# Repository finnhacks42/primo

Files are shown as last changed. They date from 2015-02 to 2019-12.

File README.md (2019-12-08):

KinderBot
=====

Contains design files and code for my version of the Primo robotic platform for young kids www.primo.io licenced under CC by-nc-sa 4.0 International
## Components
### Board
   - laser cut xxx and yyy in 3mm ply or bamboo
   - laser cut zzz in 1.5mm clear acrylic
   - 3d print 4 off zzz
   - 1 colorsense PCB
   - Arduino mega
   - HC05 serial bluetooth module
   - 16 rgb leds
   - 16 red leds

### Robot
   - Kinder surprise egg
   - laser cut zzz of 3mm ply
   - Arduino pro micro 
   - 2 gear motors 3-6V with tyres
   - HC05 serial bluetooth module
   - H-Bridge IC (sn75441one)
   - 1.1K resistor
   - 1.2K resistor
   - 2 12pin female header
   - 2 2pin male header
   - Battery holder for 4xAA

## Pairing Bluetooth modules
Once you have all your components ready, the first step set up the two HC-05 bluetooth modules to automatically pair with one another when they are turned on. We do this now as it is easier to setup and debug with both Arduinos handy than when they are plugged into the board/robot. We will configure the module for the board as the master and the module for the robot as the slave. 

   1) Get a permanent marker and write S for slave on one module and M for master on the other. Do it now, trust me, otherwise you will configure them and then forget which is which.
   2) Using the Arduino pro-micro for your bot, construct the circuit below on a breadboard.

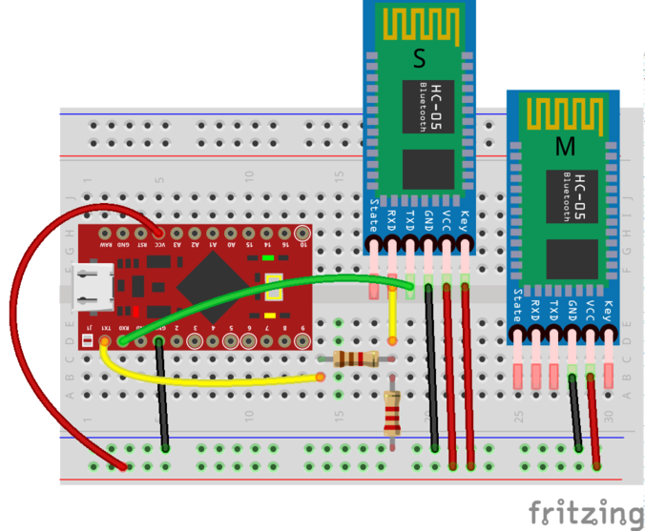
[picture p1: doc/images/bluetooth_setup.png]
bluetooth setup


Note that different manufacturers of the HC-05 breakout boards have used slightly different variants of pin orderings. On my board they `key` pin is not broken out. To temporally pull it high while programming the chip in AT mode I have just wedged a jumper wire under the protective plastic coating. Alternatively you can solder a wire directly to the pad on the bluetooth chip (see image below).

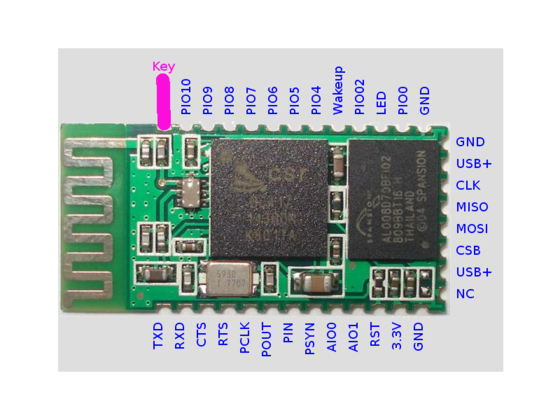
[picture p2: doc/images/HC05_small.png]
hc05


   3) Load the [bluetooth setup script](/code/bluetooth/bluetoothSetup/bluetoothSetup.ino) onto the arduino and open the serial monitor. If all goes well you should get an output like this:
   
   4) Copy the address of the slave into a text editor and replace all : with ,
   
   5) Unplug the arduino and swap the position of the master and slave modules. Edit the bluetooth setup script to setup the master module and re-upload the script to the arduino. Again if all goes well you should see ...
   
### Debugging
The bluetooth modules are setup by first putting them in AT mode and then sending AT commands to configure them. The script simply sends AT commands from the Arduino to the bluetooth module. If the steps above did not work ...
   1) Check if the module is in AT mode. If the module being configured (the one closest to the breadboard) is sucessfully in AT mode it should be flashing slowly ~ once per second when powered. If both modules are flashing rapidly, double check the wiring to the key pin. Ensure that the key pin is connected before you power up the module. 
   2) If the module is flashing slowly but you get nothing back from the AT commands check that RX/TX are wired correctly. TX0 on the arduino should be connected to RX on the bluetooth and RX0 on the arduino to TX on the bluetooth module.
   3) If the module is flashing slowly but you get garbage printed in the serial monitor, check that you serial termial baud rate is set to 9600 and line ending to NL & CR.
   4) If the module is flashing slowly but some AT command errors try running the script again. If that fails you may have to experiment with a different sequence of AT commands see xxx for an explaination of AT codes. 

## Assembly

### Board

### Robot

## Programming & Calibration

### Board

### Robot

We now need to

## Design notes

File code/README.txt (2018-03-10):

Ensure circuit board is properly secured before beginning calibration.

Rough order of steps to callibrate the board.

First test indicator leds are working.

Then test rgb leds are working

Then test light dependent resistors are working

Then upload colorsense and run python script to learn colors - paste results into primoOpticalBoard

Upload code to primoOpticalBoard - and you should correctly be identifying the tiles and sending out code.

TODO: update color_distance.py to use utils and to work from the board or a file.

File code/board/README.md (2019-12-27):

# Board 

## Assembly

## Test & Configure

   1. Run `indicatorLEDTest_PCB` and check each red indicator LED flashes in turn. 

   2. Place a tile in each slot in the board (doesn't matter what colour). Run `LDRTest` and open up the serial monitor (at 9600 baud). You should see something like:

      ```  python
      0,610
      0,758
      0,637
      0,554
      0,580
      0,536
      0,786
      0,708
      0,609
      0,549
      0,510
      0,556
      0,722
      1,731
      0,771
      0,735
      ```
      These numbers are the values of each LDR with the corresponding RGB-LED on/off respectively. The first number should be < 10 and the second > 150.

   3. Load the `CalibrateColours` sketch onto the board and run `python read.py` in the terminal. You should see `PLEASE SET BOARD TO CONFIGURATION: Red|Green|Blue|Yellow. Press any key to continue` in the terminal. This means set the board up like this:

   4. When the terminal reports `Shuffle. Press any key to continue`, move the tiles around so that each tile is in a new spot - but within the same column (ie which colour is in which column is unchanged). 

   5. Continue for each board configuration. This generates the data from which to compute what LDR responses correspond to each colour of tile.  When all is complete, you should get an output like this;

      ```
      int average_brightness[16][3] = {
         {507,588,256},
         {684,687,365},
         {709,643,295},
         {652,670,342},
         {694,410,420},
         {625,439,460},
         {696,508,496},
         {590,361,339},
         {710,606,282},
         {651,661,333},
         {627,663,366},
         {660,632,309},
         {615,520,90},
         {650,661,304},
         {715,699,371},
         {681,559,277},
      };
      
      int centers[4][3] = {
         {-75,14,114},
         {-91,-31,-40},
         {72,-62,-43},
         {94,78,-31},
      };
      ```

   6. Copy and past these values into the `RobotControl` Arduino script. You should now be able to set up the board, put tiles in and see (on the serial monitor) the correct command being sent when the button is pushed.

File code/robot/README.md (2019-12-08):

## Robot

1. Start with `kinderbot_simple`. This script just uses wheel speed & timing to approximate 90 degree turns. 
2. Check that the bluetooth chips are pairing (you should see them switch from continuous fast flashing to a slower, double flash) and instructions are being received correctly.
3. Tweak the wheel speeds & timing to get reasonable driving
4. If you are feeling adventurous, `kinderbot` was an attempt to use an inertial sensor to get nice straight driving & neat corners. It almost worked but I never managed to get rid of some random noise when reading from the sensor - which threw everything off.

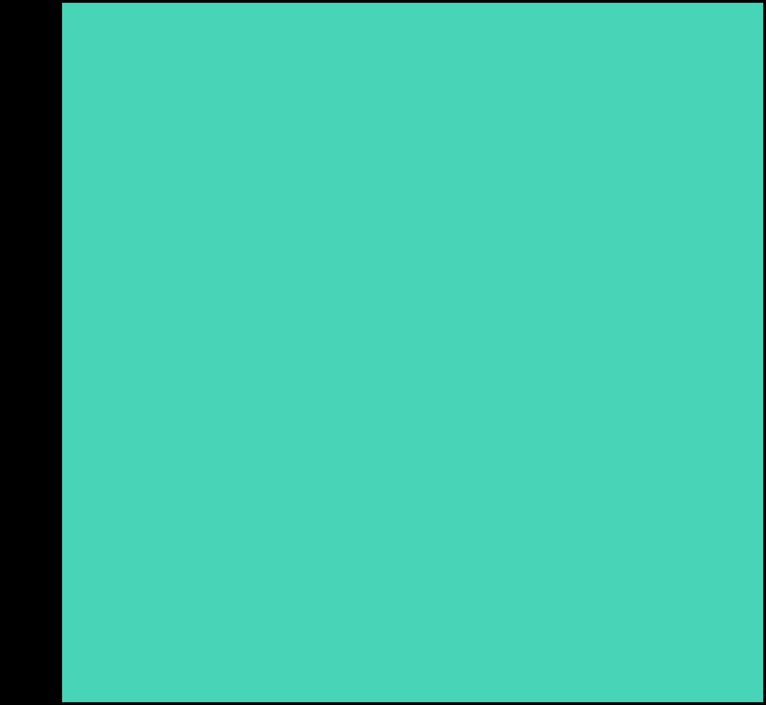
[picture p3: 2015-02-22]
hardware/blueboard/gerbers/outp5_traced.png

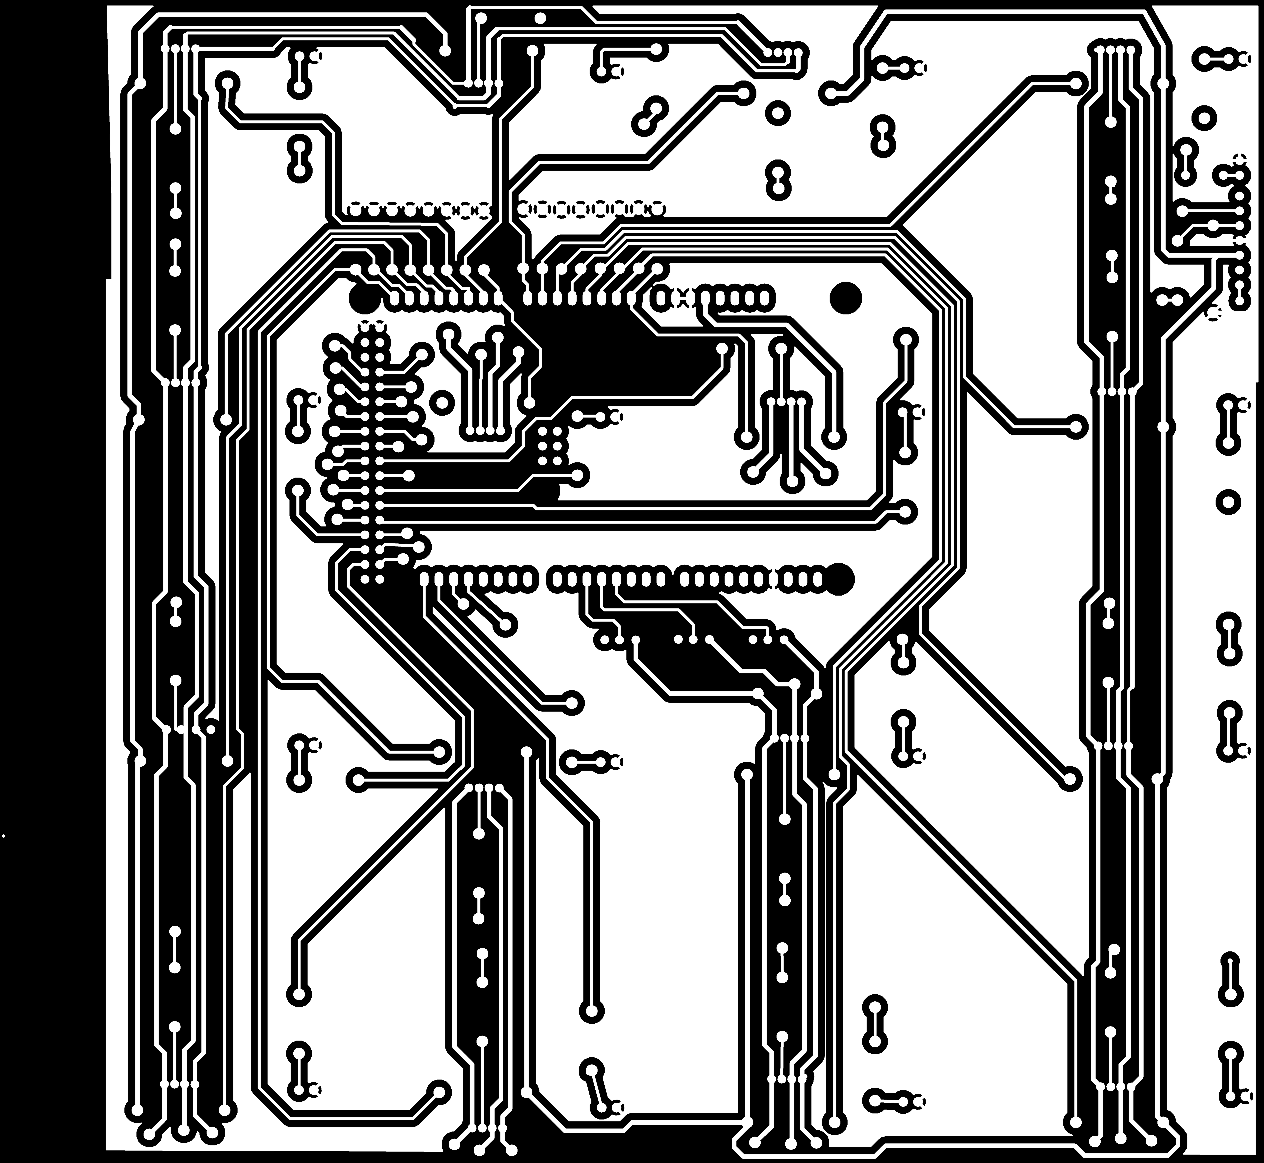
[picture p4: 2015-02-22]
hardware/blueboard/gerbers/outp0_original_back.png

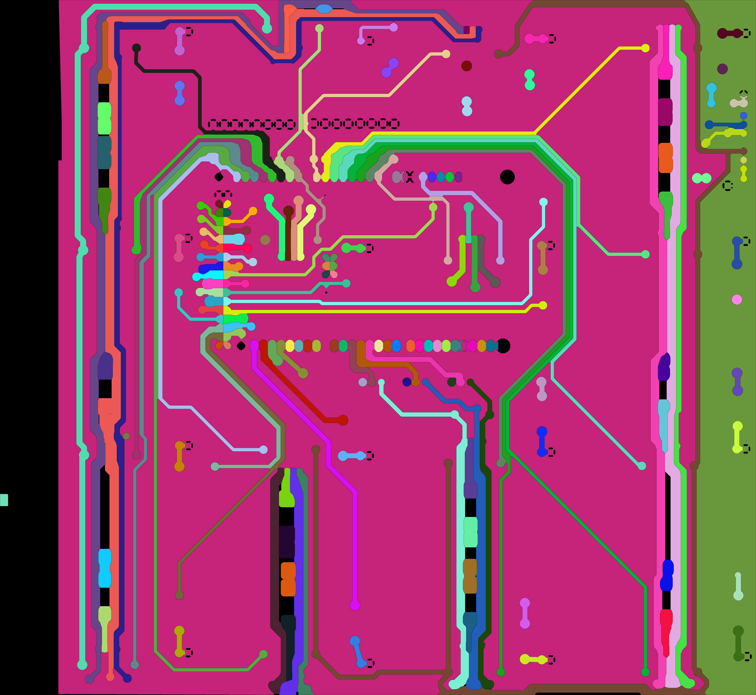
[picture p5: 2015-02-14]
hardware/blueboard/gerbers/prev/outp1_traced.png

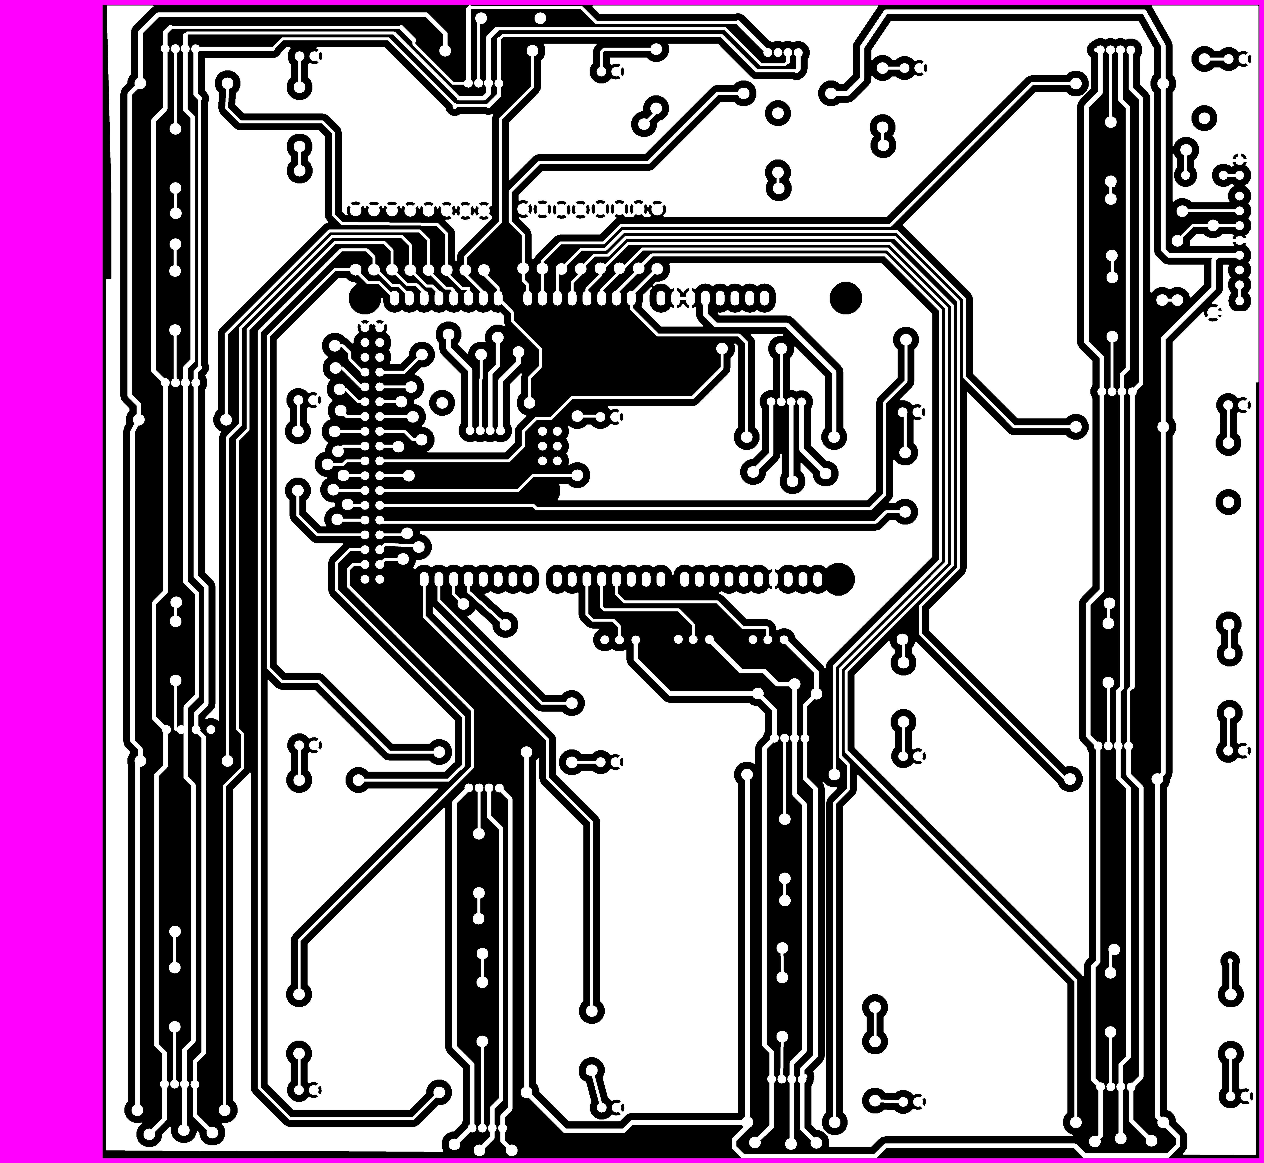
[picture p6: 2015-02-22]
hardware/blueboard/gerbers/outp3_masked.png

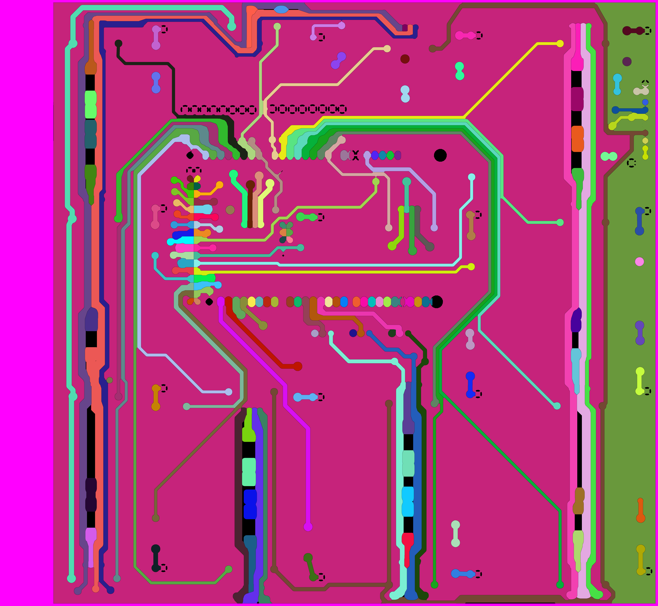
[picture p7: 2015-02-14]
hardware/blueboard/gerbers/prev/outp4_traced.png

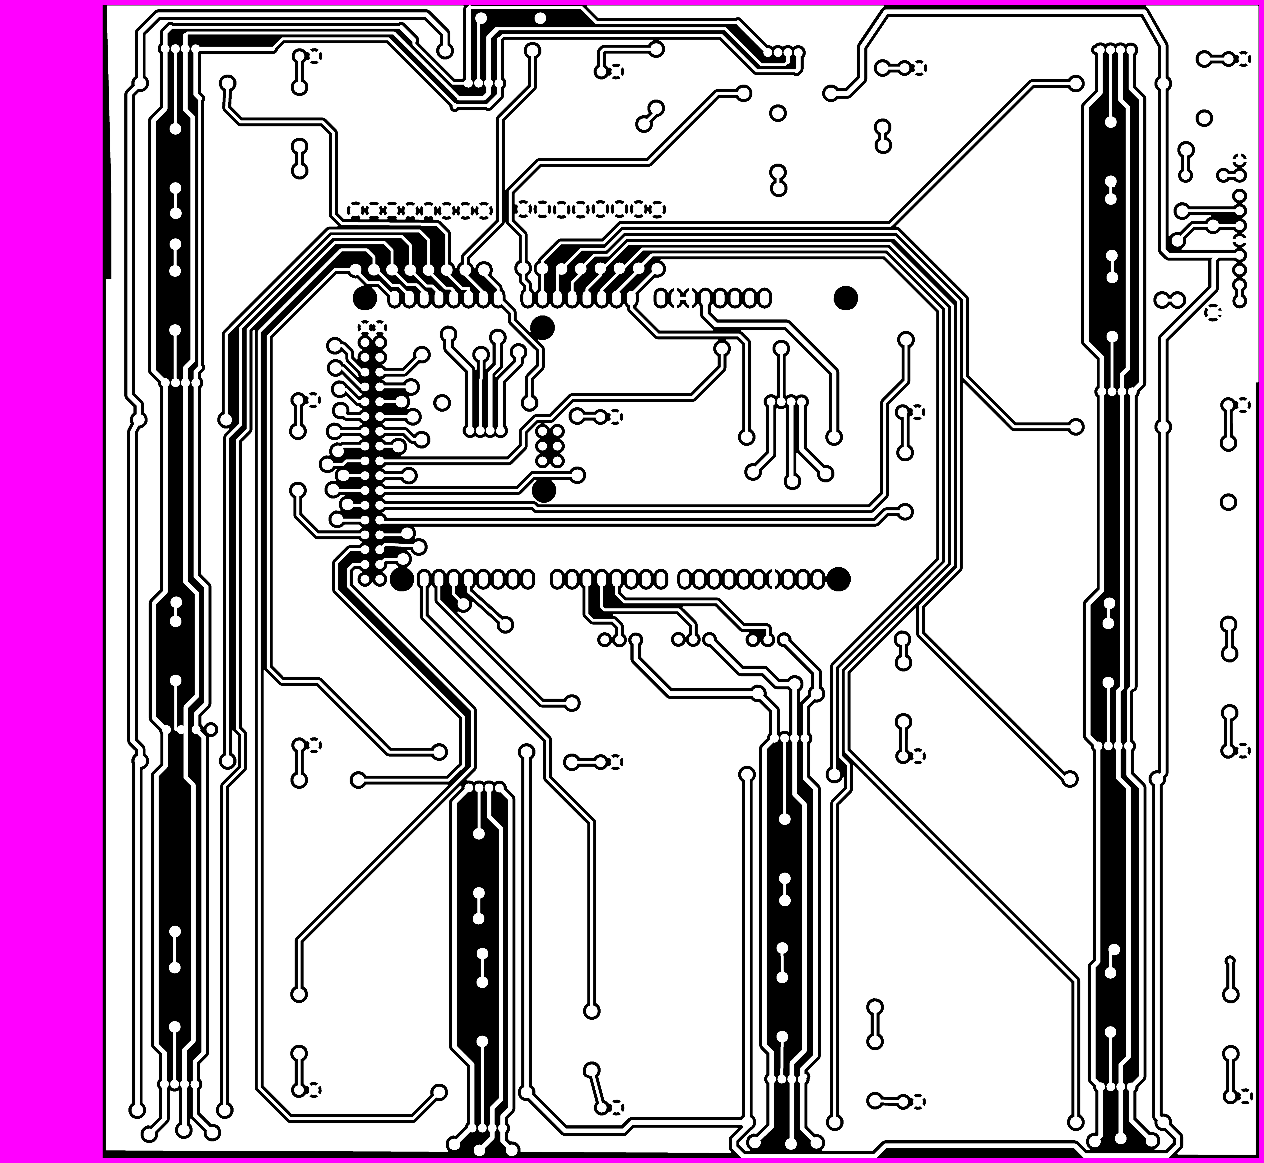
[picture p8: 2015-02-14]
hardware/blueboard/gerbers/prev/outp3_masked.png

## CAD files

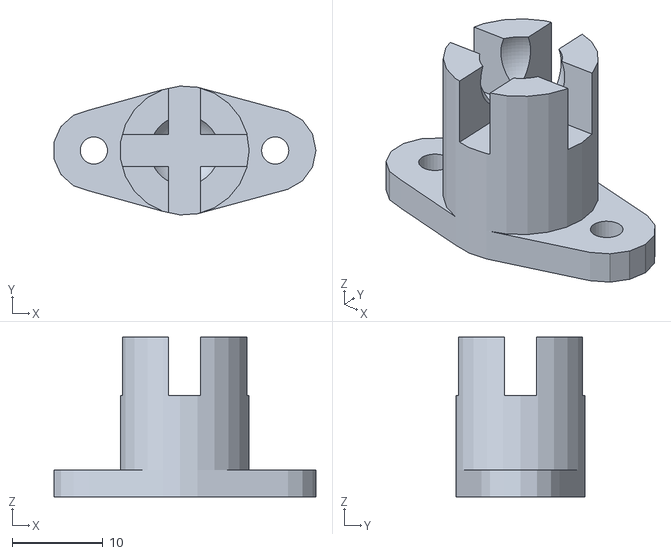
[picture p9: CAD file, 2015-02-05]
ballcasters/Ball_Caster_V2/primo5.stl
28.9 x 14.2 x 17.6

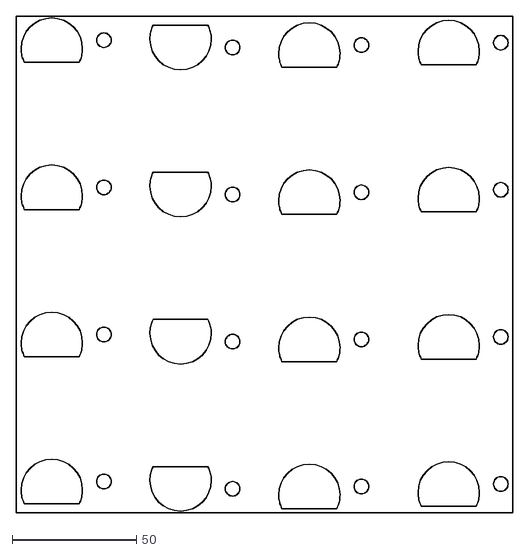
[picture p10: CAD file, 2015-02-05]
hardware/blueboard/board_outline.dxf
199.9 x 199.9

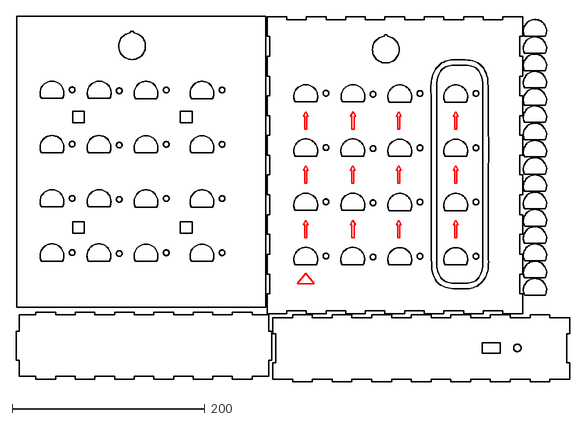
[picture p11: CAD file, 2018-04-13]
laser_cut/board/board_sheet1.dxf
574.0 x 379.6

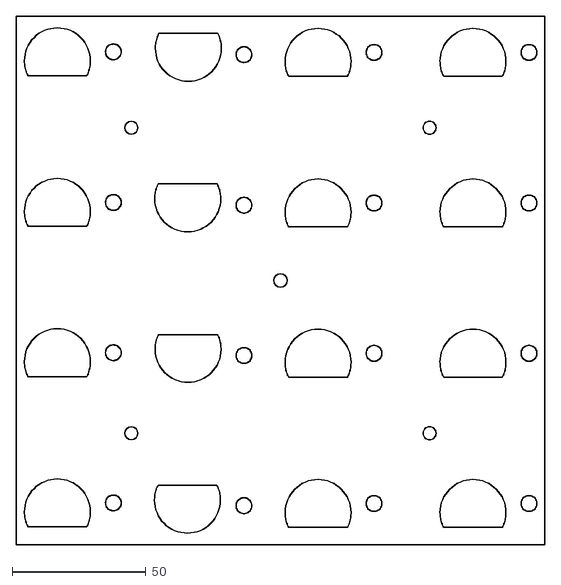
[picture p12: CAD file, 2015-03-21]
laser_cut/board/circuit/circuit5.dxf
197.9 x 197.9

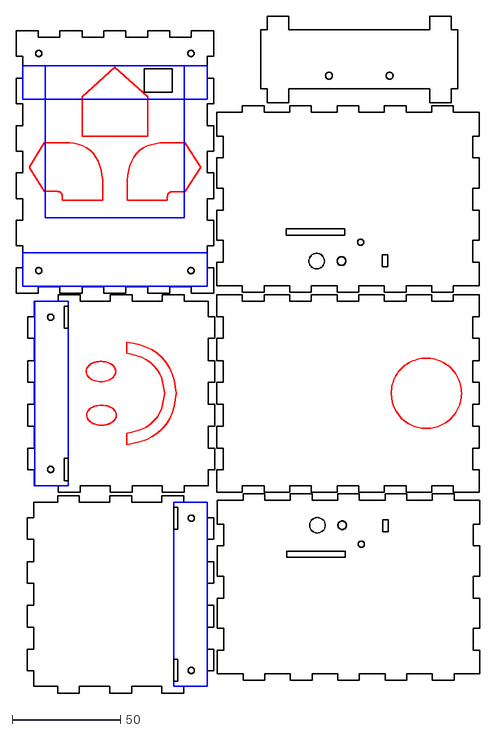
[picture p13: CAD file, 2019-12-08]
laser_cut/robot/robot.dxf
213.8 x 312.1

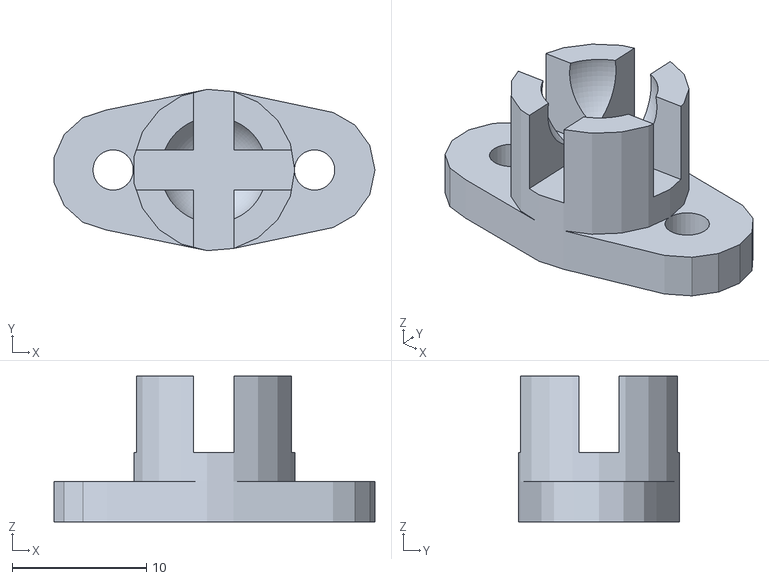
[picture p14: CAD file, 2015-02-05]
ballcasters/Ball_Caster_V2/primo2.stl
23.9 x 12.0 x 10.9

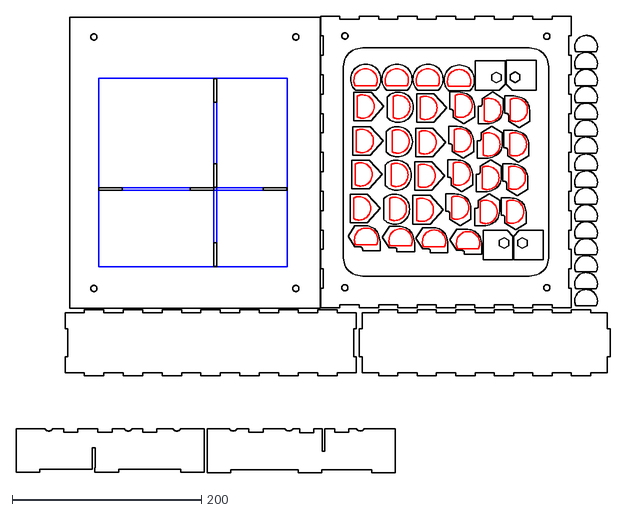
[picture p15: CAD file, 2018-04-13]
laser_cut/board/board_sheet2_with_cross_support.dxf
627.9 x 482.3

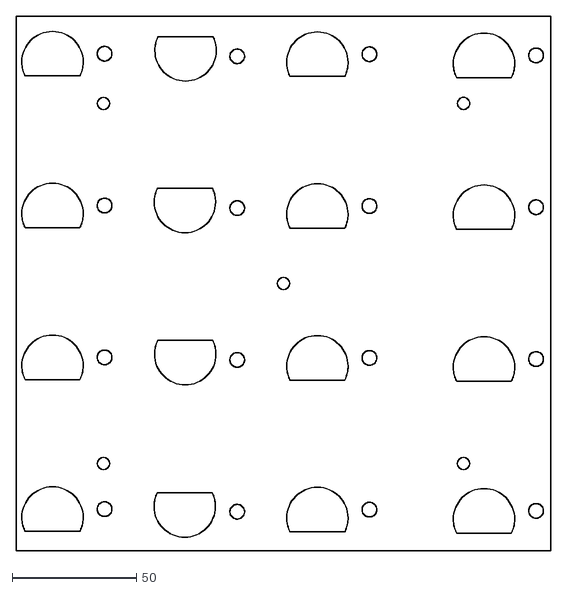
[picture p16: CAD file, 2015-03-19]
laser_cut/board/circuit/circuit4.dxf
215.1 x 215.1

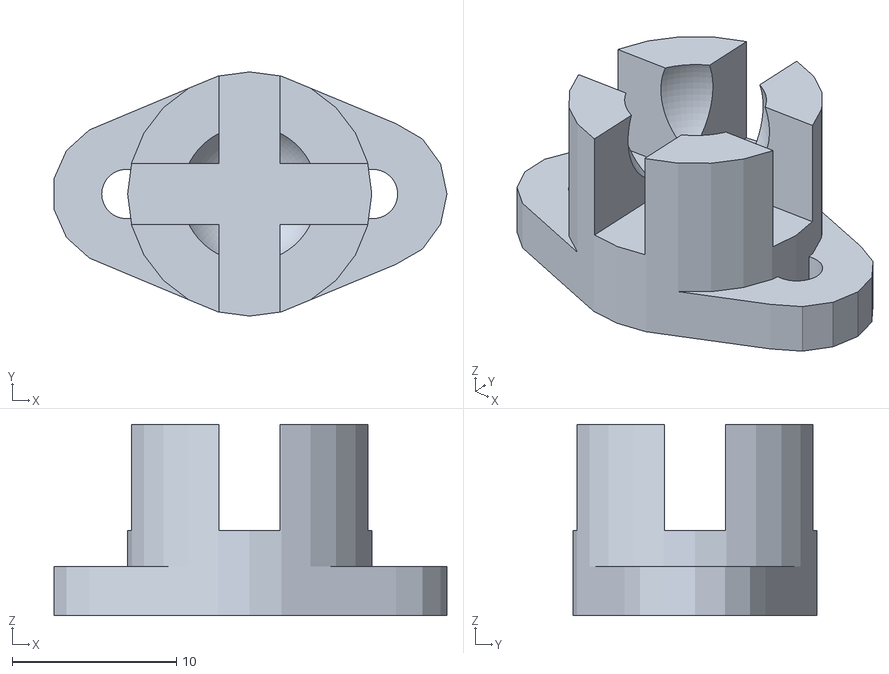
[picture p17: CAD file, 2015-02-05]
ballcasters/Ball_Caster_V2/primo1.stl
23.9 x 14.8 x 11.6

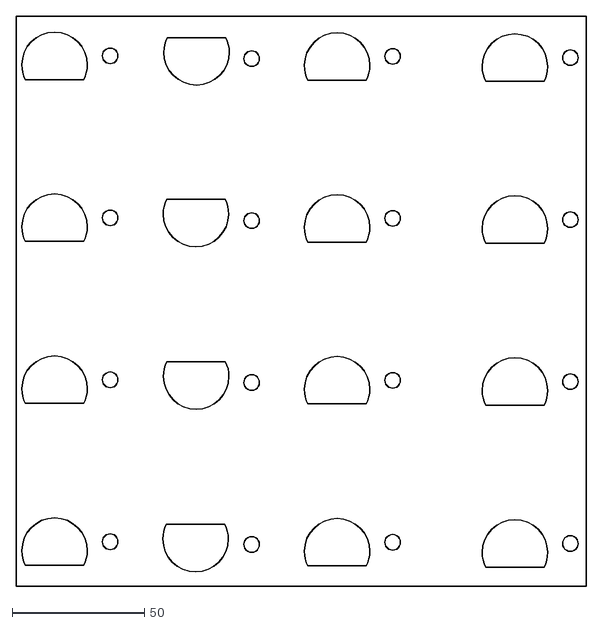
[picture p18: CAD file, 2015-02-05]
laser_cut/board/circuit/circuit.dxf
215.1 x 215.1

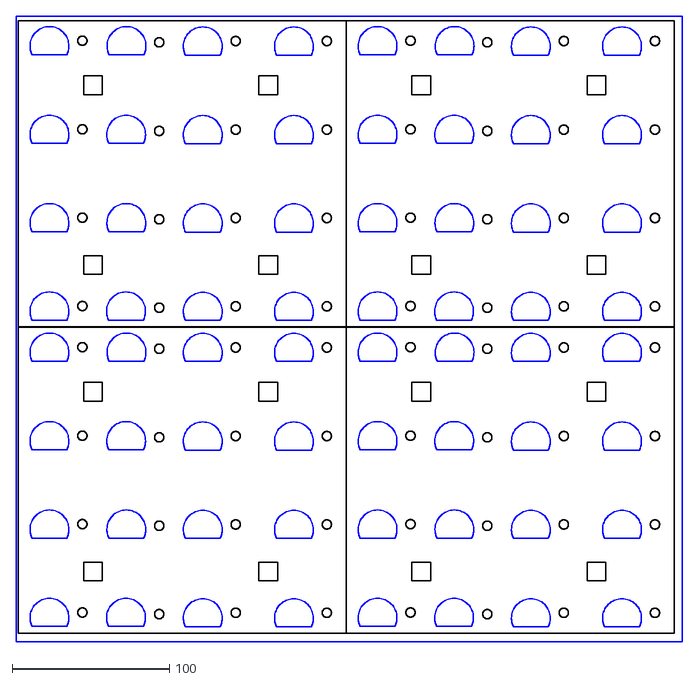
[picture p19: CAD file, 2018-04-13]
laser_cut/board/clear_acrylic.dxf
423.8 x 398.4

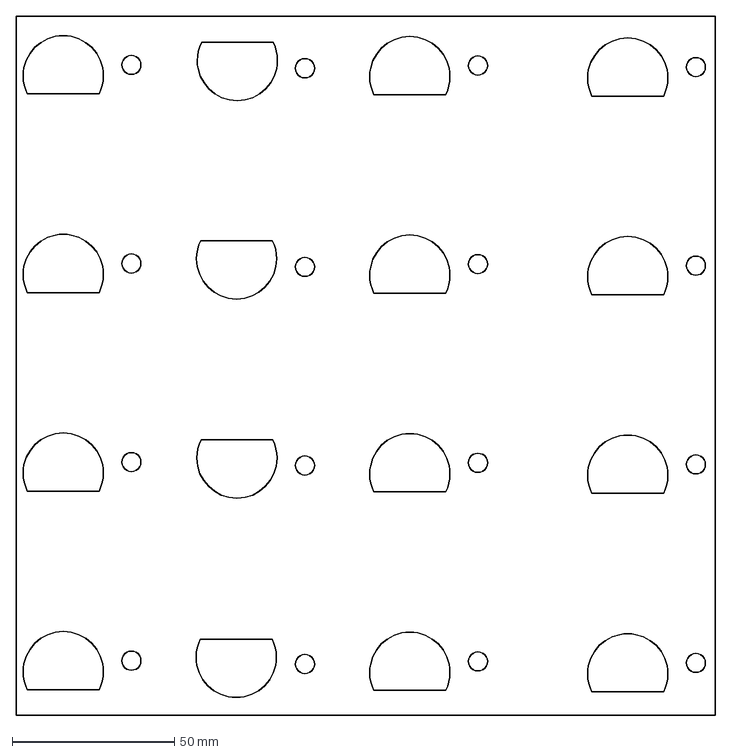
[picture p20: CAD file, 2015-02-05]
laser_cut/board/circuit/circuit2.dxf
215.1 x 215.1 mm

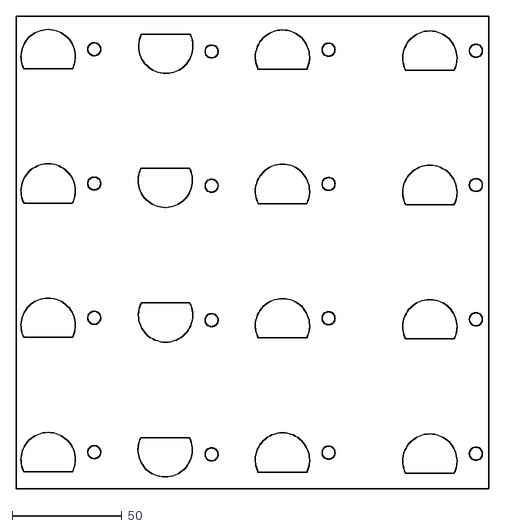
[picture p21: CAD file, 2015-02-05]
laser_cut/board/circuit/circuit3.dxf
215.1 x 215.1

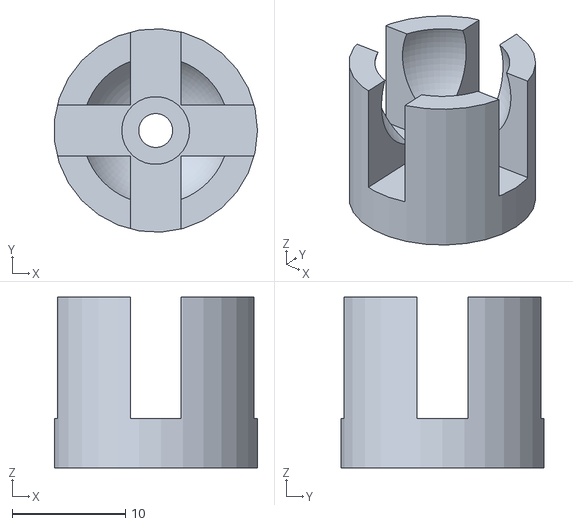
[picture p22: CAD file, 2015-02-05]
ballcasters/Ball_Caster_V2/BallCasterV2_1.stl
17.9 x 18.0 x 15.1

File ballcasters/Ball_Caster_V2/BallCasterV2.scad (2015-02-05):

WallThickness = 3;
//BallSize = 13; te ruim
//BallSize = 12.7; bijna
//BallSize = 12.4;goed
BallSize = 7.85;
Airgap = .2;
Mount = 3;
TotalHeight = 20; 		//this includes the ball
MountScrewRad = 1.5;  	//3mm screw
BallProtrude = .30; 	//percentage of ball radius sticking out 
ScrewSpacing = 20;		//spaceing of the mountholes center to center
MountMiddle = false; 	//mount int the center
MountBase = true;		//use mount base 2 holes


cylrad = (BallSize/2) + WallThickness + Airgap;
echo (cylrad);


difference()
{
	union()
	{
		ball_mount ();
		if(MountBase)
		{		
			base();
		}
	}
	if(MountMiddle)
	{
		cylinder(r1 = MountScrewRad, r2 = MountScrewRad, h= TotalHeight,center=true, $fn=30);
		translate([0,0,(TotalHeight-BallSize)/2]) 
		{
			cylinder(r1 = MountScrewRad*2, r2 = MountScrewRad*2, h= TotalHeight, $fn=30);
		}
	}
}

module ball_mount ()
{
	difference () 
	{
		cylinder(r1 = cylrad , r2 = cylrad,  TotalHeight - (BallSize*BallProtrude));
	
		translate([0,0,TotalHeight - BallSize/2]) 
		{
			cube(size = [cylrad*2+5, cylrad/2, BallSize*1.25], center = true );
			rotate([0,0,90]) cube(size = [cylrad*2+5, cylrad/2, BallSize*1.25], center = true );
		}
	
		translate([0,0,TotalHeight - (BallSize/2)]) 
		{
			sphere (BallSize/2+Airgap, $fa=5, $fs=0.1);
		}
	}
}
module base()
{
	difference (){
		linear_extrude(height=Mount)
		hull() {
			translate([ScrewSpacing/2,0,0]) {
				circle(  MountScrewRad*3);
			}
			translate([0-ScrewSpacing/2,0,0]) {
				circle( MountScrewRad*3);
			}
			circle( cylrad);
		}
	
		translate([ScrewSpacing/2,0,-1]) {
			#cylinder(r1 = MountScrewRad, r2 = MountScrewRad, h= Mount+2,$fn=30);
		}
		translate([0-ScrewSpacing/2,0,-1]) {
			#cylinder(r1 = MountScrewRad, r2 = MountScrewRad, h= Mount+2,$fn=30);
			
		}
	}
}

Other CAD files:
ballcasters/Ball_Caster_V2/primo3.stl
ballcasters/Ball_Caster_V2/primo4.stl
ballcasters/Ball_Caster_V2/BallCasterV2.stl

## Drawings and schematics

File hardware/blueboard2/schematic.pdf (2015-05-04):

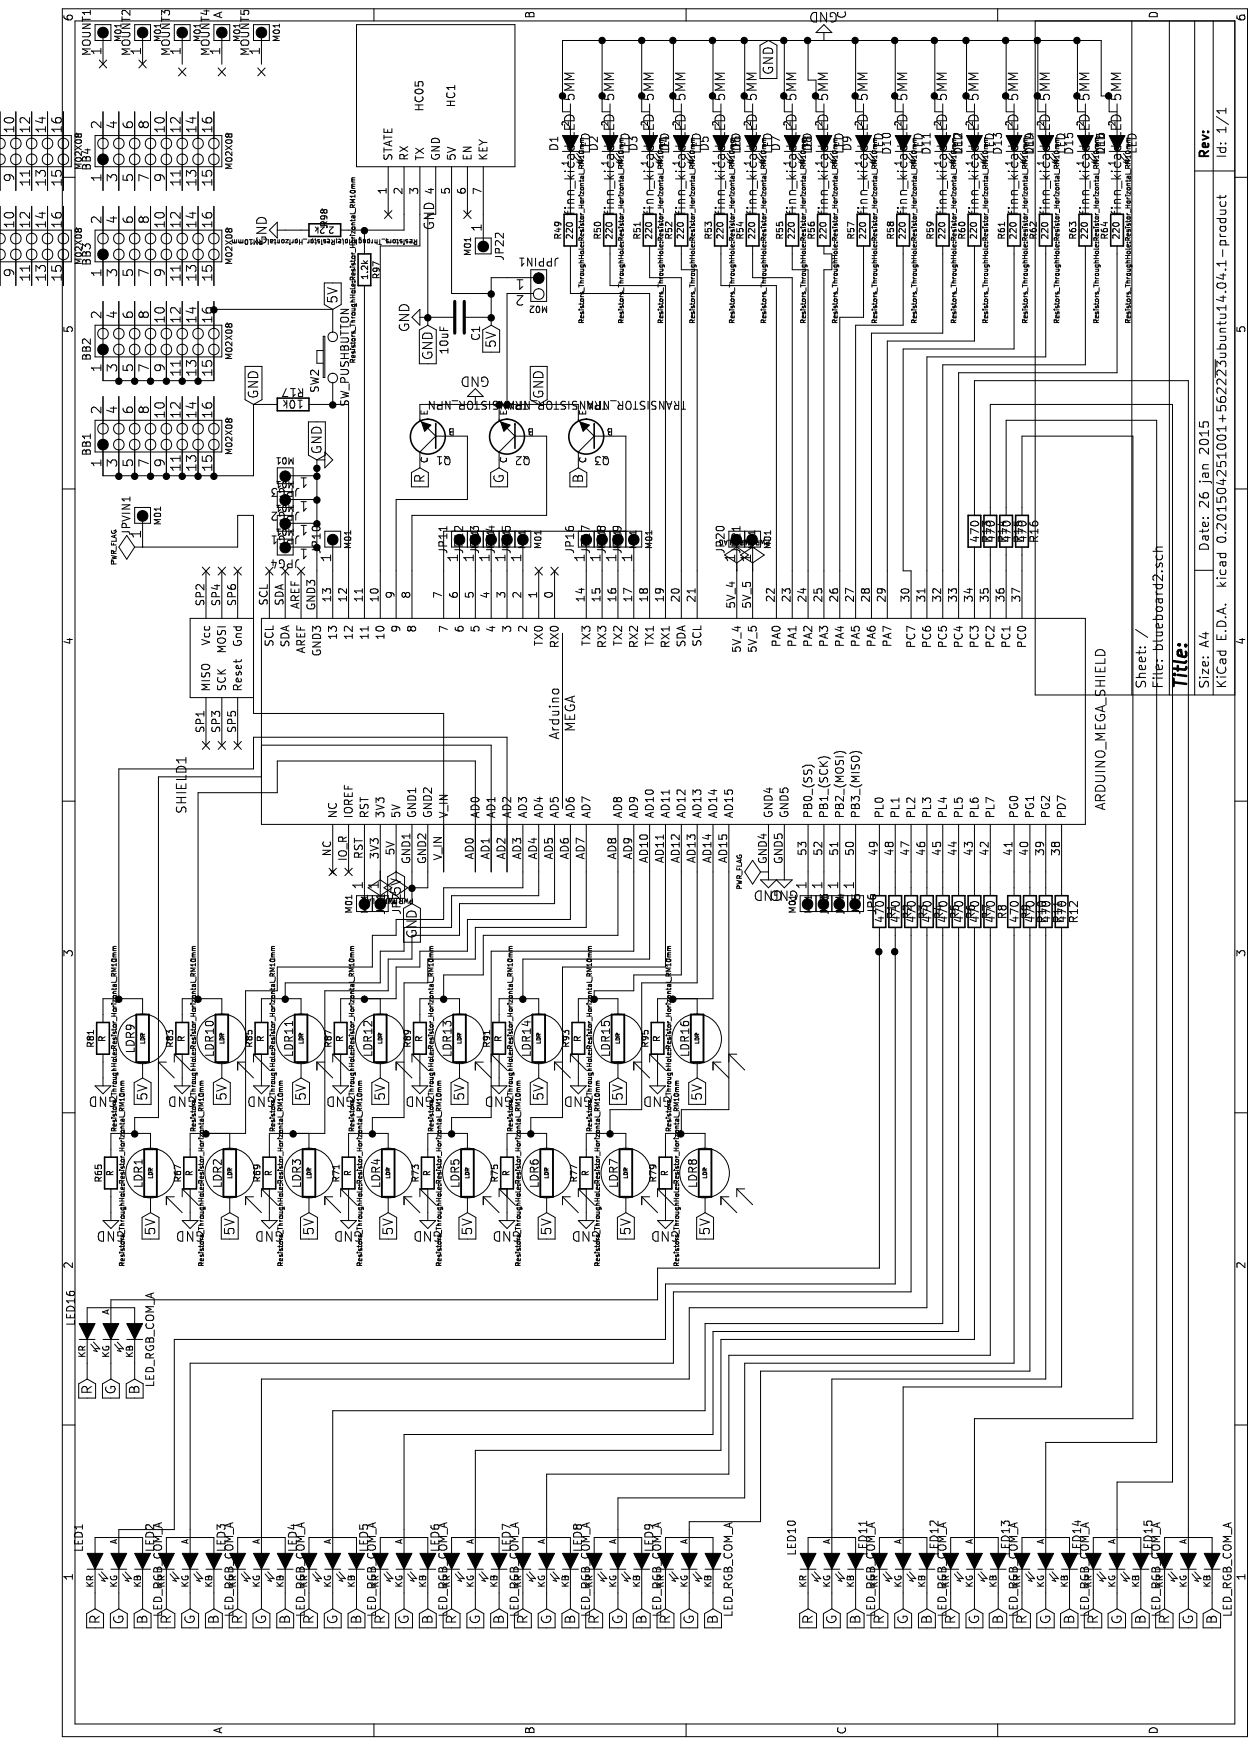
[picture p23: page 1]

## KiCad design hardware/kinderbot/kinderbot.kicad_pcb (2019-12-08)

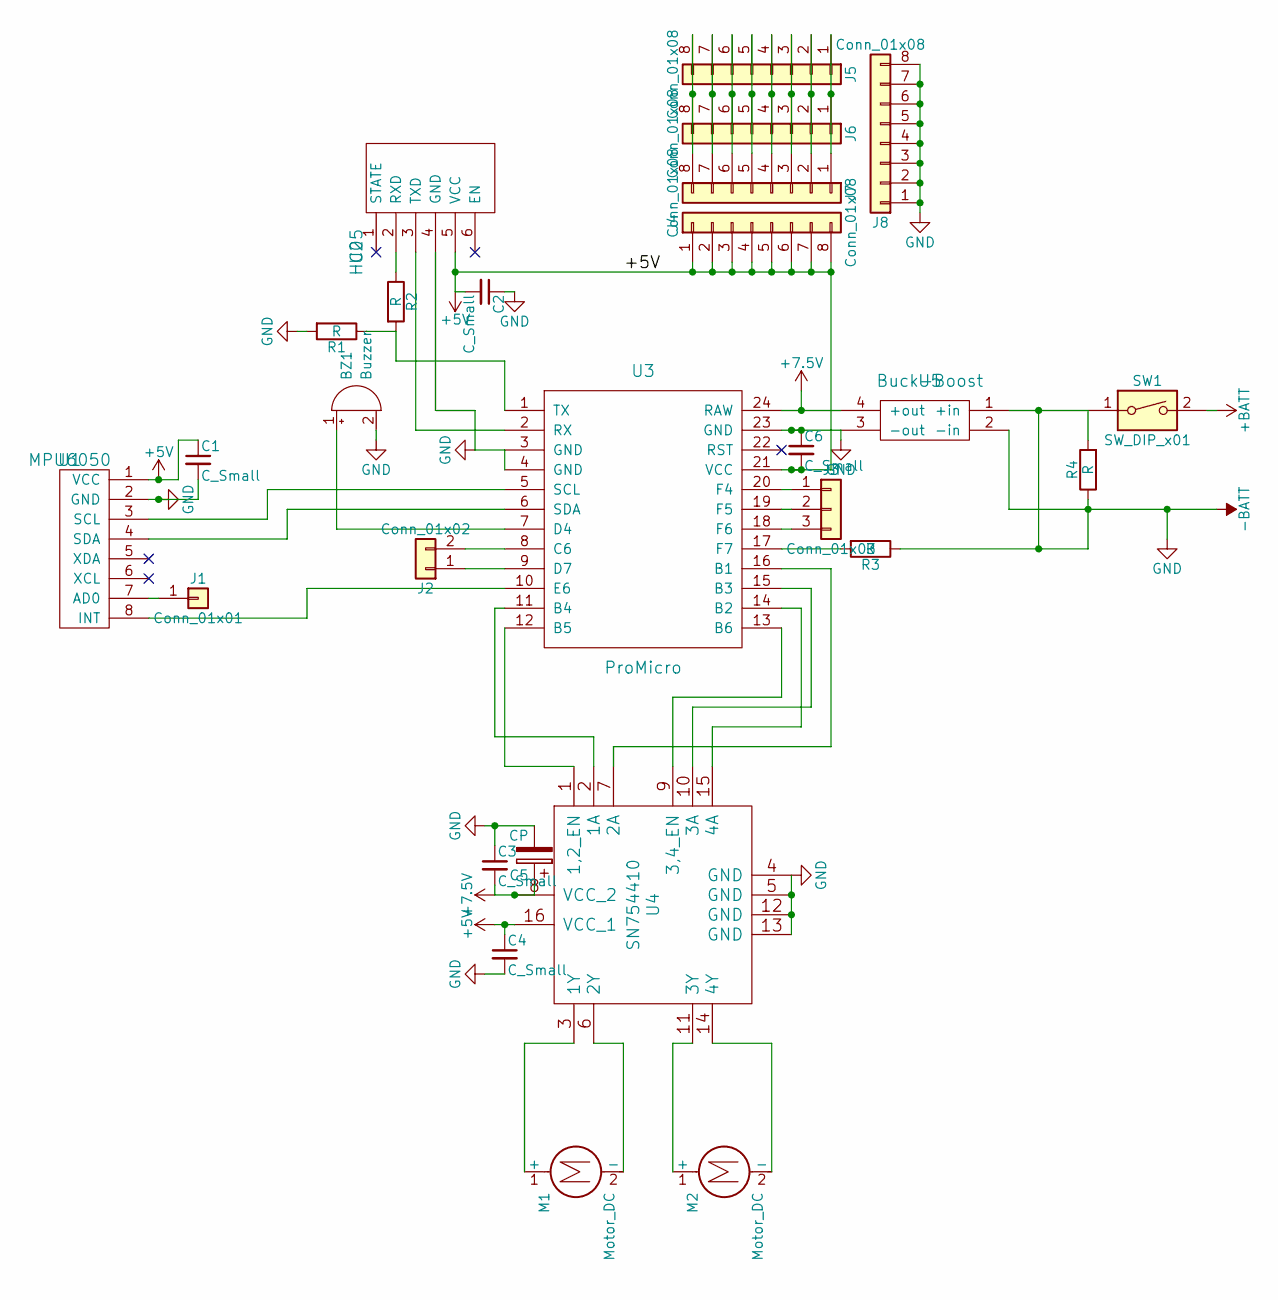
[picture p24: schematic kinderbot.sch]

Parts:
BZ1: Buzzer; BUZZER
C1, C2, C3, C4, C6: C_Small; CP_Radial_D4.0mm_P1.50mm
C5: CP; CP_Radial_D4.0mm_P2.00mm
J1: Conn_01x01; Pin_Header_Straight_1x01_Pitch2.54mm
J2: Conn_01x02; Pin_Header_Straight_1x02_Pitch2.54mm
J3: Conn_01x03; Pin_Header_Straight_1x03_Pitch2.54mm
J4, J5, J6, J7, J8: Conn_01x08; Pin_Header_Straight_1x08_Pitch2.54mm
M1, M2: Motor_DC; Pin_Header_Straight_1x02_Pitch2.54mm
R1, R2, R3, R4: R; R_Axial_DIN0207_L6.3mm_D2.5mm_P10.16mm_Horizontal
SW1: SW_DIP_x01; Pin_Header_Straight_1x02_Pitch2.54mm
U1: MPU6050; Pin_Header_Straight_1x08_Pitch2.54mm
U2: HC05; Pin_Header_Straight_1x06_Pitch2.54mm
U3: ProMicro
U4: SN754410; DIP-16_W7.62mm
U5: Buck-Boost; Pin_Header_Straight_2x02_Pitch2.54mm

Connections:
+5V: C1.1, C2.2, C4.1, C6.2, J4.1, J4.2, J4.3, J4.4, J4.5, J4.6, J4.7, J4.8, U1.1 (VCC), U2.5 (VCC), U3.21 (VCC), U4.16 (VCC_1)
+7.5V: C3.2, C5.1, U3.24 (RAW), U4.8 (VCC_2), U5.4 (+out)
+BATT: SW1.2
-BATT: BZ1.2 (+), C1.2, C2.1, C3.1, C4.2, C5.2, C6.1, J8.1, J8.2, J8.3, J8.4, J8.5, J8.6, J8.7, J8.8, R1.2, R3.1, R4.1, R4.2, SW1.1, U1.2 (GND), U2.4 (GND), U3.3 (GND), U3.4 (GND), U3.23 (GND), U4.4 (GND), U4.5 (GND), U4.12 (GND), U4.13 (GND), U5.1 (+in), U5.2 (-in), U5.3 (-out)
unnamed: BZ1.1 (-), U3.7 (D4)
unnamed: J1.1, U1.7 (AD0)
unnamed: J2.1, U3.9 (D7)
unnamed: J2.2, U3.8 (C6)
unnamed: J3.1, U3.20 (F4)
unnamed: J3.2, U3.19 (F5)
unnamed: J3.3, U3.18 (F6)
unnamed: J5.1, J6.1, J7.1
unnamed: J5.2, J6.2, J7.2
unnamed: J5.3, J6.3, J7.3
unnamed: J5.4, J6.4, J7.4
unnamed: J5.5, J6.5, J7.5
unnamed: J5.6, J6.6, J7.6
unnamed: J5.7, J6.7, J7.7
unnamed: J5.8, J6.8, J7.8
unnamed: M1.1 (+), U4.3 (1Y)
unnamed: M1.2 (-), U4.6 (2Y)
unnamed: M2.1 (+), U4.11 (3Y)
unnamed: M2.2 (-), U4.14 (4Y)
unnamed: R1.1, R2.2, U3.1 (TX)
unnamed: R2.1, U2.2 (RXD)
unnamed: R3.2, U3.17 (F7)
unnamed: U1.3 (SCL), U3.5 (SCL)
unnamed: U1.4 (SDA), U3.6 (SDA)
unnamed: U1.8 (INT), U3.10 (E6)
unnamed: U2.3 (TXD), U3.2 (RX)
unnamed: U3.11 (B4), U4.2 (1A)
unnamed: U3.12 (B5), U4.1 (1,2_EN)
unnamed: U3.13 (B6), U4.9 (3,4_EN)
unnamed: U3.14 (B2), U4.15 (4A)
unnamed: U3.15 (B3), U4.10 (3A)
unnamed: U3.16 (B1), U4.7 (2A)

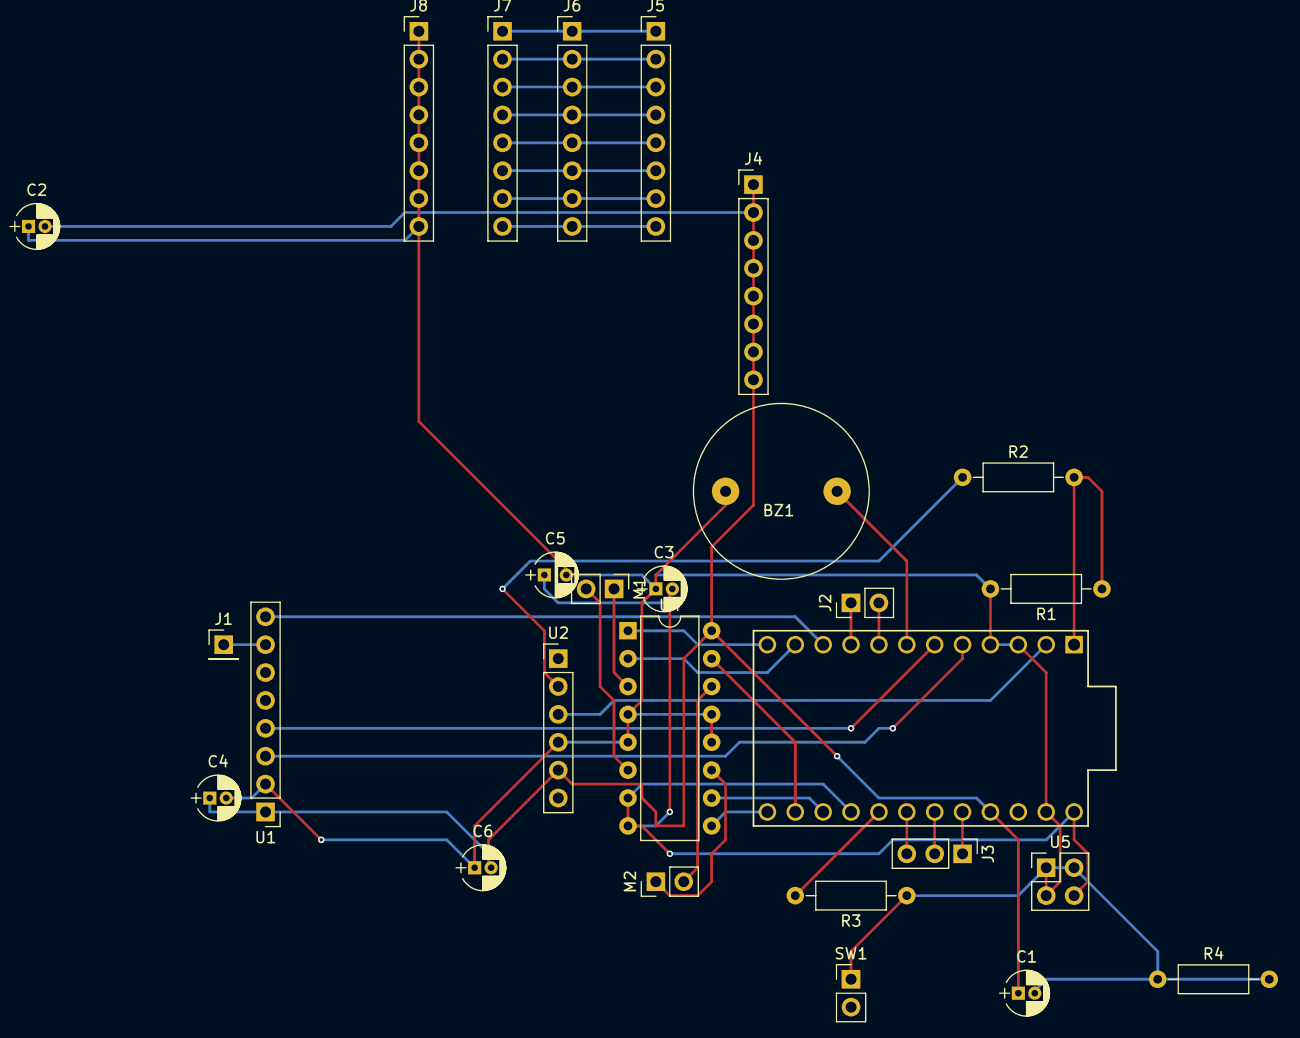
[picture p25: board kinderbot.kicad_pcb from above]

Board: 2 copper layers, 27 parts (0 on the bottom side), 35 nets.

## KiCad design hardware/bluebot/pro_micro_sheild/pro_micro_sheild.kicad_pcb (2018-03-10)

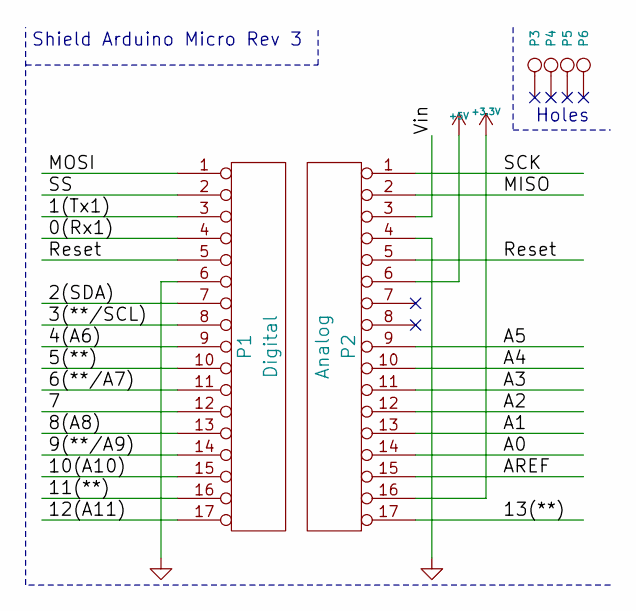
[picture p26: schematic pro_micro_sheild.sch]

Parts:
P1: Digital; Socket_Strip_Arduino_1x17
P2: Analog; Socket_Strip_Arduino_1x17
P3, P4, P5, P6: CONN_1; 1pin_Micro

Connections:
+3V3: P2.16
+5V: P2.6
/0(Rx1): P1.4
/1(Tx1): P1.3
/2(SDA): P1.7
/3(**/SCL): P1.8
/4(A6): P1.9
/5(**): P1.10
/6(**/A7): P1.11
/7: P1.12
/8(A8): P1.13
/9(**/A9): P1.14
/10(A10): P1.15
/11(**): P1.16
/12(A11): P1.17
/13(**): P2.17
/A0: P2.14
/A1: P2.13
/A2: P2.12
/A3: P2.11
/A4: P2.10
/A5: P2.9
/AREF: P2.15
/MISO: P2.2
/MOSI: P1.1
/Reset: P1.5, P2.5
/SCK: P2.1
/SS: P1.2
/Vin: P2.3
GND: P1.6, P2.4

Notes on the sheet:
Shield Arduino Micro Rev 3
Holes

Board: 2 copper layers, 6 parts (0 on the bottom side), 2 nets, no tracks yet.

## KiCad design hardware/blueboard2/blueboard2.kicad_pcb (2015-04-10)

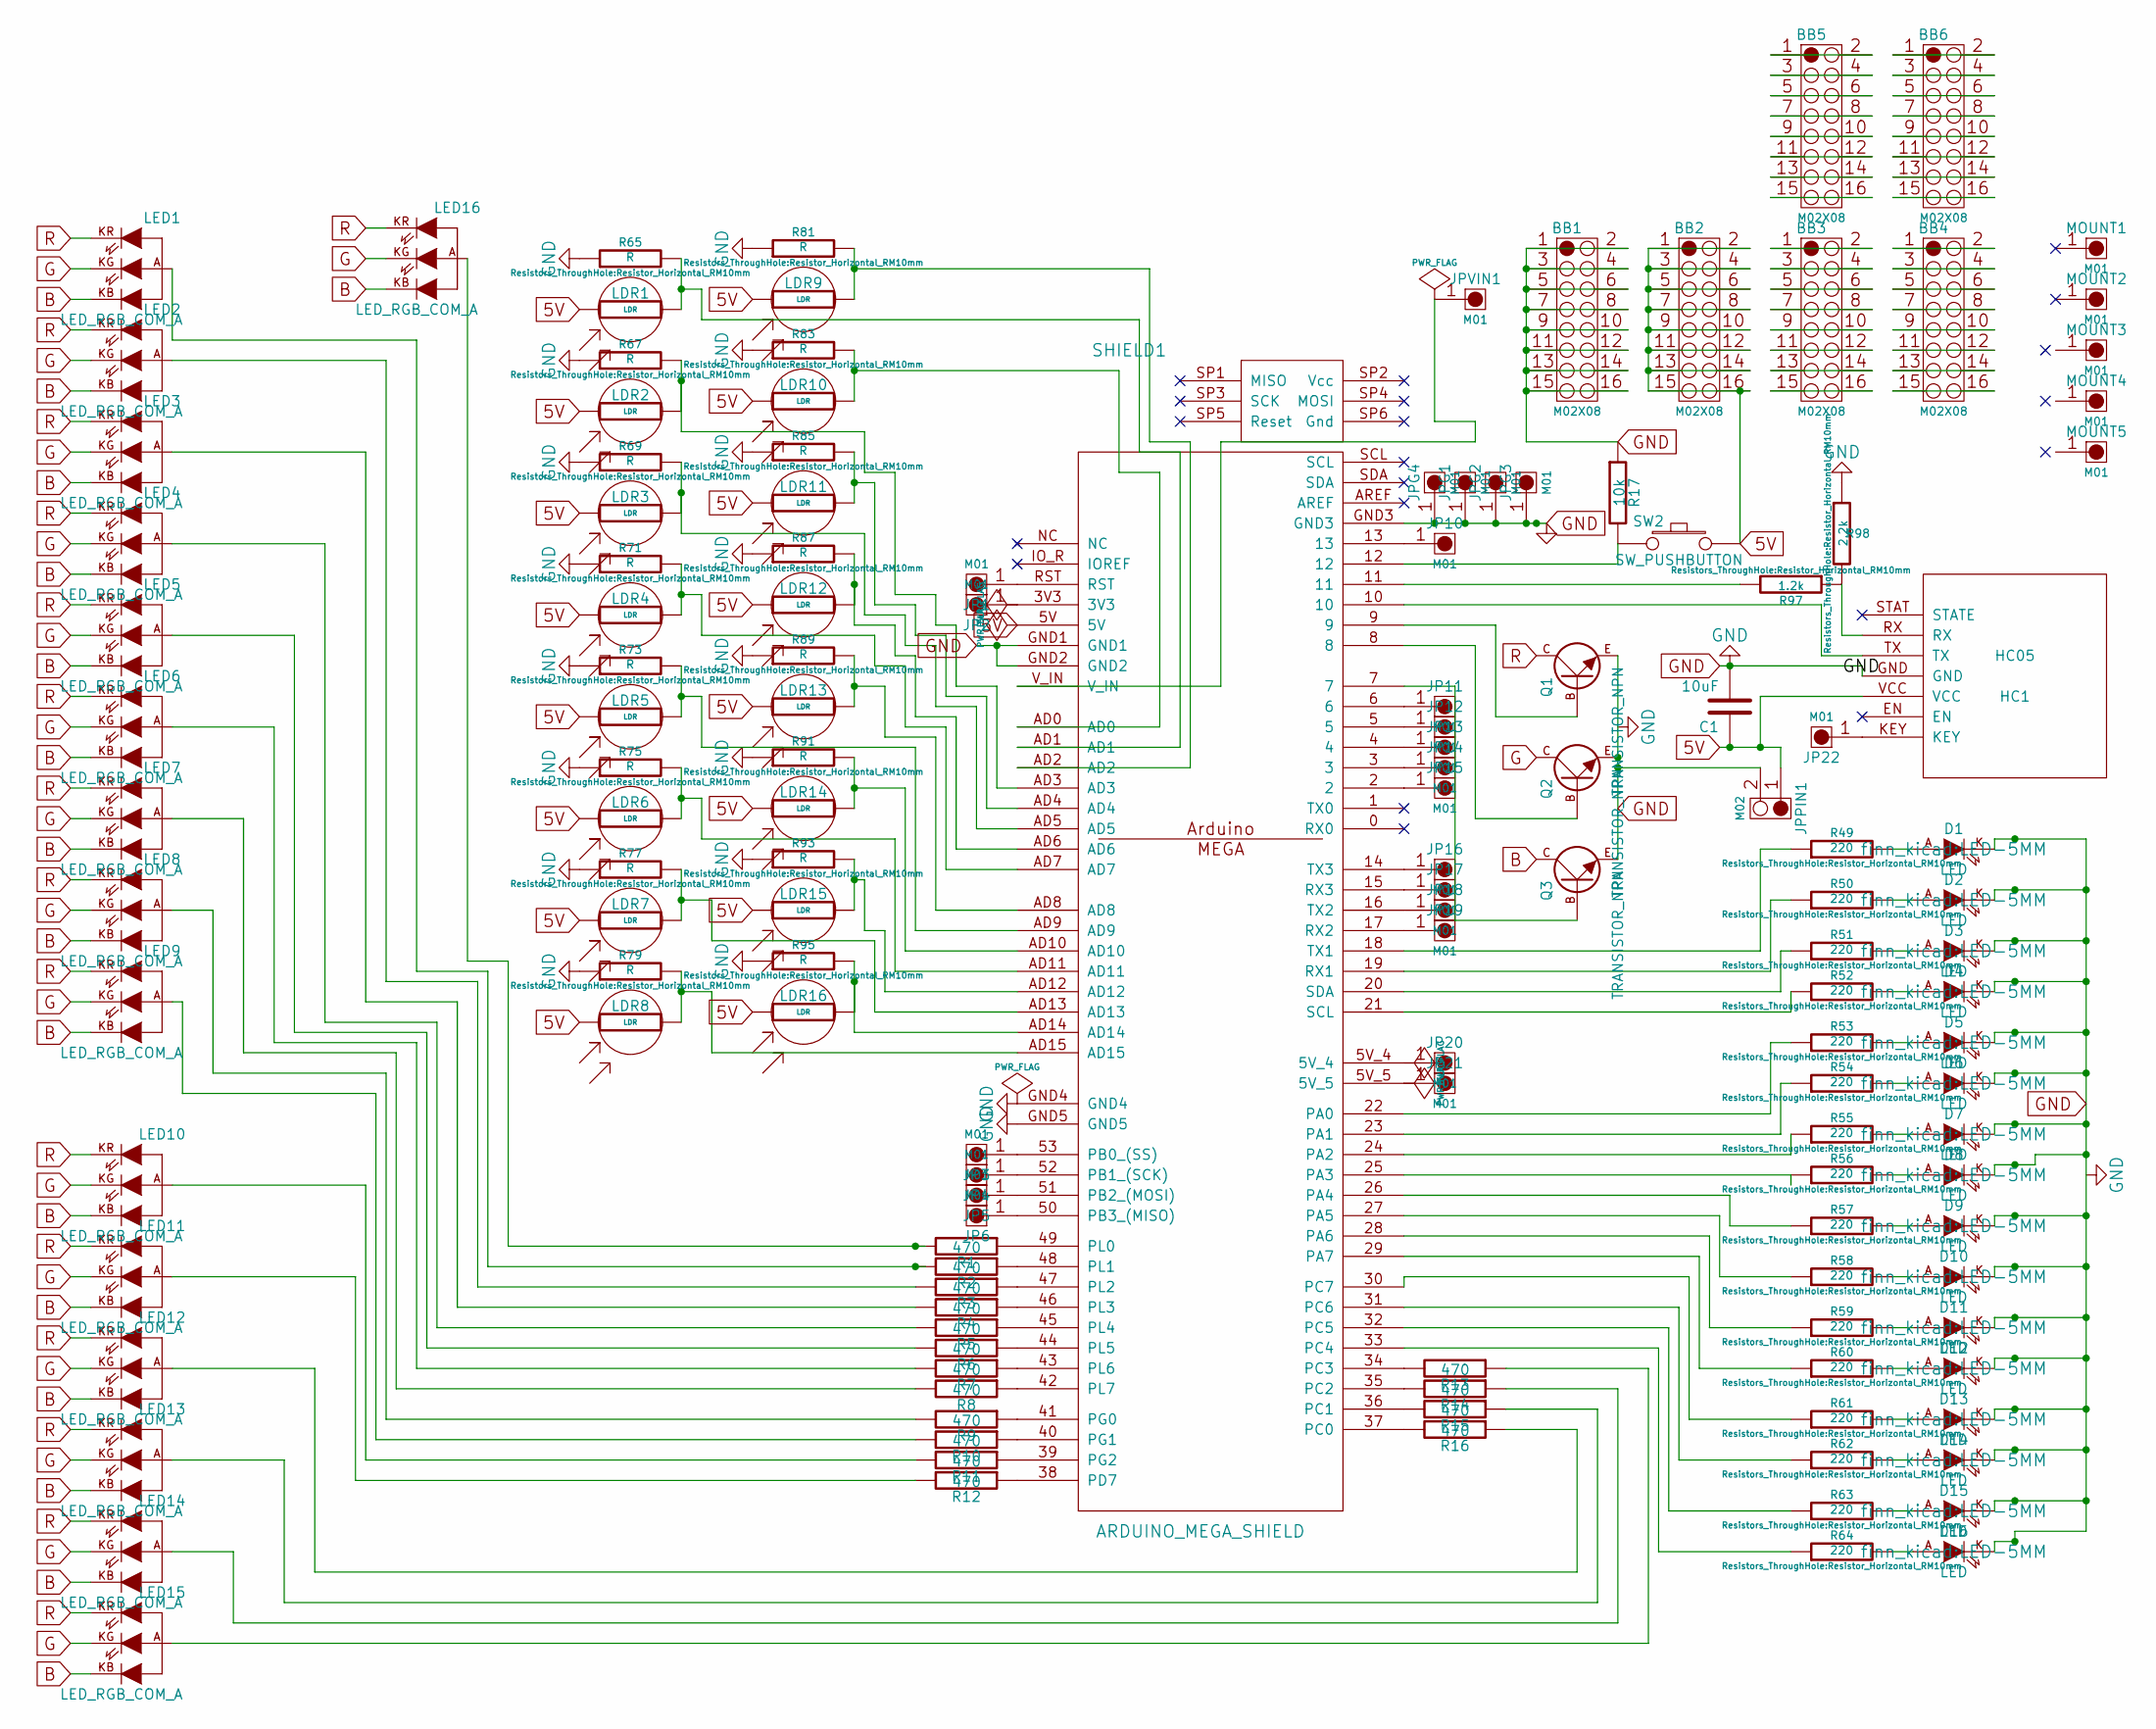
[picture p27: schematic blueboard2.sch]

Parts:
BB1, BB2, BB3, BB4, BB5, BB6: M02X08; 2X8
C1: 10uF; CAP_ELECTRO_D4S1.8
D1, D2, D3, D4, D5, D6, D7, D8, D9, D10, D11, D12, D13, D14, D15, D16: LED; LED-5MM
HC1: HC05
JP1, JP2, JP3, JP4, JP5, JP6, JP10, JP11, JP12, JP13, JP14, JP15, JP16, JP17, JP18, JP19, JP20, JP21, JP22: M01; 1X01
JPG1, JPG2, JPG3, JPG4: M01; 1X01
JPPIN1: M02; 1X02
JPVIN1: M01; 1X01
LDR1, LDR2, LDR3, LDR4, LDR5, LDR6, LDR7, LDR8, LDR9, LDR10, LDR11, LDR12, LDR13, LDR14, LDR15, LDR16: LDR; Resistor_Horizontal_RM15mm
LED1, LED2, LED3, LED4, LED5, LED6, LED7, LED8, LED9, LED10, LED11, LED12, LED13, LED14, LED15, LED16: LED_RGB_COM_A; LED-RGB-comA-5MM
MOUNT1, MOUNT2, MOUNT3, MOUNT4, MOUNT5: M01; SolderWirePad_single_2mmDrill
Q1, Q2, Q3: TRANSISTOR_NPN; EBC-transistor-NPN
R1, R2, R3, R4, R5, R6, R7, R8, R9, R10, R11, R12, R13, R14, R15, R16: 470; Resistor_Horizontal_RM10mm
R17: 10k; Resistor_Horizontal_RM10mm
R49, R50, R51, R52, R53, R54, R55, R56, R57, R58, R59, R60, R61, R62, R63, R64: 220; Resistor_Horizontal_RM10mm
R65, R67, R69, R71, R73, R75, R77, R79, R81, R83, R85, R87, R89, R91, R93, R95: R; Resistor_Horizontal_RM10mm
R97: 1.2k; Resistor_Horizontal_RM10mm
R98: 2.2k; Resistor_Horizontal_RM10mm
SHIELD1: ARDUINO_MEGA_SHIELD
SW2: SW_PUSHBUTTON; 1X02

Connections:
5V: BB2.1, BB2.2, BB2.3, BB2.4, BB2.5, BB2.6, BB2.7, BB2.8, BB2.9, BB2.10, BB2.11, BB2.12, BB2.13, BB2.14, BB2.15, BB2.16, C1.1, HC1.VCC, JPPIN1.1, LDR1.1, LDR2.1, LDR3.1, LDR4.1, LDR5.1, LDR6.1, LDR7.1, LDR8.1, LDR9.1, LDR10.1, LDR11.1, LDR12.1, LDR13.1, LDR14.1, LDR15.1, LDR16.1, SHIELD1.5V, SW2.2
B: LED1.KB, LED2.KB, LED3.KB, LED4.KB, LED5.KB, LED6.KB, LED7.KB, LED8.KB, LED9.KB, LED10.KB, LED11.KB, LED12.KB, LED13.KB, LED14.KB, LED15.KB, LED16.KB, Q3.C
G: LED1.KG, LED2.KG, LED3.KG, LED4.KG, LED5.KG, LED6.KG, LED7.KG, LED8.KG, LED9.KG, LED10.KG, LED11.KG, LED12.KG, LED13.KG, LED14.KG, LED15.KG, LED16.KG, Q2.C
GND: BB1.1, BB1.2, BB1.3, BB1.4, BB1.5, BB1.6, BB1.7, BB1.8, BB1.9, BB1.10, BB1.11, BB1.12, BB1.13, BB1.14, BB1.15, BB1.16, C1.2, D1.K, D2.K, D3.K, D4.K, D5.K, D6.K, D7.K, D8.K, D9.K, D10.K, D11.K, D12.K, D13.K, D14.K, D15.K, D16.K, HC1.GND, JPG1.1, JPG2.1, JPG3.1, JPG4.1, JPPIN1.2, Q1.E, Q2.E, Q3.E, R17.1, R65.1, R67.1, R69.1, R71.1, R73.1, R75.1, R77.1, R79.1, R81.1, R83.1, R85.1, R87.1, R89.1, R91.1, R93.1, R95.1, R98.1, SHIELD1.GND1, SHIELD1.GND2, SHIELD1.GND3, SHIELD1.GND4, SHIELD1.GND5
unnamed: BB3.1, BB3.2
unnamed: BB3.3, BB3.4
unnamed: BB3.5, BB3.6
unnamed: BB3.7, BB3.8
unnamed: BB3.9, BB3.10
unnamed: BB3.11, BB3.12
unnamed: BB3.13, BB3.14
unnamed: BB3.15, BB3.16
unnamed: BB4.1, BB4.2
unnamed: BB4.3, BB4.4
unnamed: BB4.5, BB4.6
unnamed: BB4.7, BB4.8
unnamed: BB4.9, BB4.10
unnamed: BB4.11, BB4.12
unnamed: BB4.13, BB4.14
unnamed: BB4.15, BB4.16
unnamed: BB5.1, BB5.2
unnamed: BB5.3, BB5.4
unnamed: BB5.5, BB5.6
unnamed: BB5.7, BB5.8
unnamed: BB5.9, BB5.10
unnamed: BB5.11, BB5.12
unnamed: BB5.13, BB5.14
unnamed: BB5.15, BB5.16
unnamed: BB6.1, BB6.2
unnamed: BB6.3, BB6.4
unnamed: BB6.5, BB6.6
unnamed: BB6.7, BB6.8
unnamed: BB6.9, BB6.10
unnamed: BB6.11, BB6.12
unnamed: BB6.13, BB6.14
unnamed: BB6.15, BB6.16
unnamed: D1.A, R49.2
unnamed: D2.A, R50.2
unnamed: D3.A, R51.2
unnamed: D4.A, R52.2
unnamed: D5.A, R53.2
unnamed: D6.A, R54.2
unnamed: D7.A, R55.2
unnamed: D8.A, R56.2
unnamed: D9.A, R57.2
unnamed: D10.A, R58.2
unnamed: D11.A, R59.2
unnamed: D12.A, R60.2
unnamed: D13.A, R61.2
unnamed: D14.A, R62.2
unnamed: D15.A, R63.2
unnamed: D16.A, R64.2
unnamed: HC1.KEY, JP22.1
unnamed: HC1.RX, R97.1, R98.2
unnamed: HC1.TX, SHIELD1.10
unnamed: JP1.1, SHIELD1.RST
unnamed: JP2.1, SHIELD1.3V3
unnamed: JP3.1, SHIELD1.53 (PB0_(SS))
unnamed: JP4.1, SHIELD1.52 (PB1_(SCK))
unnamed: JP5.1, SHIELD1.51 (PB2_(MOSI))
unnamed: JP6.1, SHIELD1.50 (PB3_(MISO))
unnamed: JP10.1, SHIELD1.13
unnamed: JP11.1, SHIELD1.6
unnamed: JP12.1, SHIELD1.5
unnamed: JP13.1, SHIELD1.4
unnamed: JP14.1, SHIELD1.3
unnamed: JP15.1, SHIELD1.2
unnamed: JP16.1, SHIELD1.14 (TX3)
unnamed: JP17.1, SHIELD1.15 (RX3)
unnamed: JP18.1, SHIELD1.16 (TX2)
unnamed: JP19.1, SHIELD1.17 (RX2)
unnamed: JP20.1, SHIELD1.5V_4
unnamed: JP21.1, SHIELD1.5V_5
unnamed: JPVIN1.1, SHIELD1.V_IN
unnamed: LDR1.2, R65.2, SHIELD1.AD1
unnamed: LDR2.2, R67.2, SHIELD1.AD3
unnamed: LDR3.2, R69.2, SHIELD1.AD5
unnamed: LDR4.2, R71.2, SHIELD1.AD7
unnamed: LDR5.2, R73.2, SHIELD1.AD9
unnamed: LDR6.2, R75.2, SHIELD1.AD11
unnamed: LDR7.2, R77.2, SHIELD1.AD13
unnamed: LDR8.2, R79.2, SHIELD1.AD15
unnamed: LDR9.2, R81.2, SHIELD1.AD2
unnamed: LDR10.2, R83.2, SHIELD1.AD0
unnamed: LDR11.2, R85.2, SHIELD1.AD4
unnamed: LDR12.2, R87.2, SHIELD1.AD6
unnamed: LDR13.2, R89.2, SHIELD1.AD8
unnamed: LDR14.2, R91.2, SHIELD1.AD10
unnamed: LDR15.2, R93.2, SHIELD1.AD12
unnamed: LDR16.2, R95.2, SHIELD1.AD14
unnamed: LED1.A, R2.2
unnamed: LED2.A, R3.2
unnamed: LED3.A, R4.2
unnamed: LED4.A, R5.2
unnamed: LED5.A, R6.2
unnamed: LED6.A, R7.2
unnamed: LED7.A, R8.2
unnamed: LED8.A, R9.2
unnamed: LED9.A, R10.2
unnamed: LED10.A, R11.2
unnamed: LED11.A, R12.2
unnamed: LED12.A, R16.1
unnamed: LED13.A, R15.1
unnamed: LED14.A, R14.1
unnamed: LED15.A, R13.1
unnamed: LED16.A, R1.2
unnamed: Q1.B, SHIELD1.9
unnamed: Q2.B, SHIELD1.8
unnamed: Q3.B, SHIELD1.7
unnamed: R1.1, SHIELD1.49 (PL0)
unnamed: R2.1, SHIELD1.48 (PL1)
unnamed: R3.1, SHIELD1.47 (PL2)
unnamed: R4.1, SHIELD1.46 (PL3)
unnamed: R5.1, SHIELD1.45 (PL4)
unnamed: R6.1, SHIELD1.44 (PL5)
unnamed: R7.1, SHIELD1.43 (PL6)
unnamed: R8.1, SHIELD1.42 (PL7)
unnamed: R9.1, SHIELD1.41 (PG0)
unnamed: R10.1, SHIELD1.40 (PG1)
unnamed: R11.1, SHIELD1.39 (PG2)
unnamed: R12.1, SHIELD1.38 (PD7)
unnamed: R13.2, SHIELD1.34 (PC3)
unnamed: R14.2, SHIELD1.35 (PC2)
unnamed: R15.2, SHIELD1.36 (PC1)
unnamed: R16.2, SHIELD1.37 (PC0)
unnamed: R17.2, SHIELD1.12, SW2.1
unnamed: R49.1, SHIELD1.18 (TX1)
unnamed: R50.1, SHIELD1.19 (RX1)
unnamed: R51.1, SHIELD1.20 (SDA)
unnamed: R52.1, SHIELD1.21 (SCL)
unnamed: R53.1, SHIELD1.22 (PA0)
unnamed: R54.1, SHIELD1.23 (PA1)
unnamed: R55.1, SHIELD1.24 (PA2)
unnamed: R56.1, SHIELD1.25 (PA3)
unnamed: R57.1, SHIELD1.26 (PA4)
unnamed: R58.1, SHIELD1.27 (PA5)
unnamed: R59.1, SHIELD1.28 (PA6)
unnamed: R60.1, SHIELD1.29 (PA7)
unnamed: R61.1, SHIELD1.30 (PC7)
unnamed: R62.1, SHIELD1.31 (PC6)
unnamed: R63.1, SHIELD1.32 (PC5)
unnamed: R64.1, SHIELD1.33 (PC4)
unnamed: R97.2, SHIELD1.11
R: LED1.KR, LED2.KR, LED3.KR, LED4.KR, LED5.KR, LED6.KR, LED7.KR, LED8.KR, LED9.KR, LED10.KR, LED11.KR, LED12.KR, LED13.KR, LED14.KR, LED15.KR, LED16.KR, Q1.C

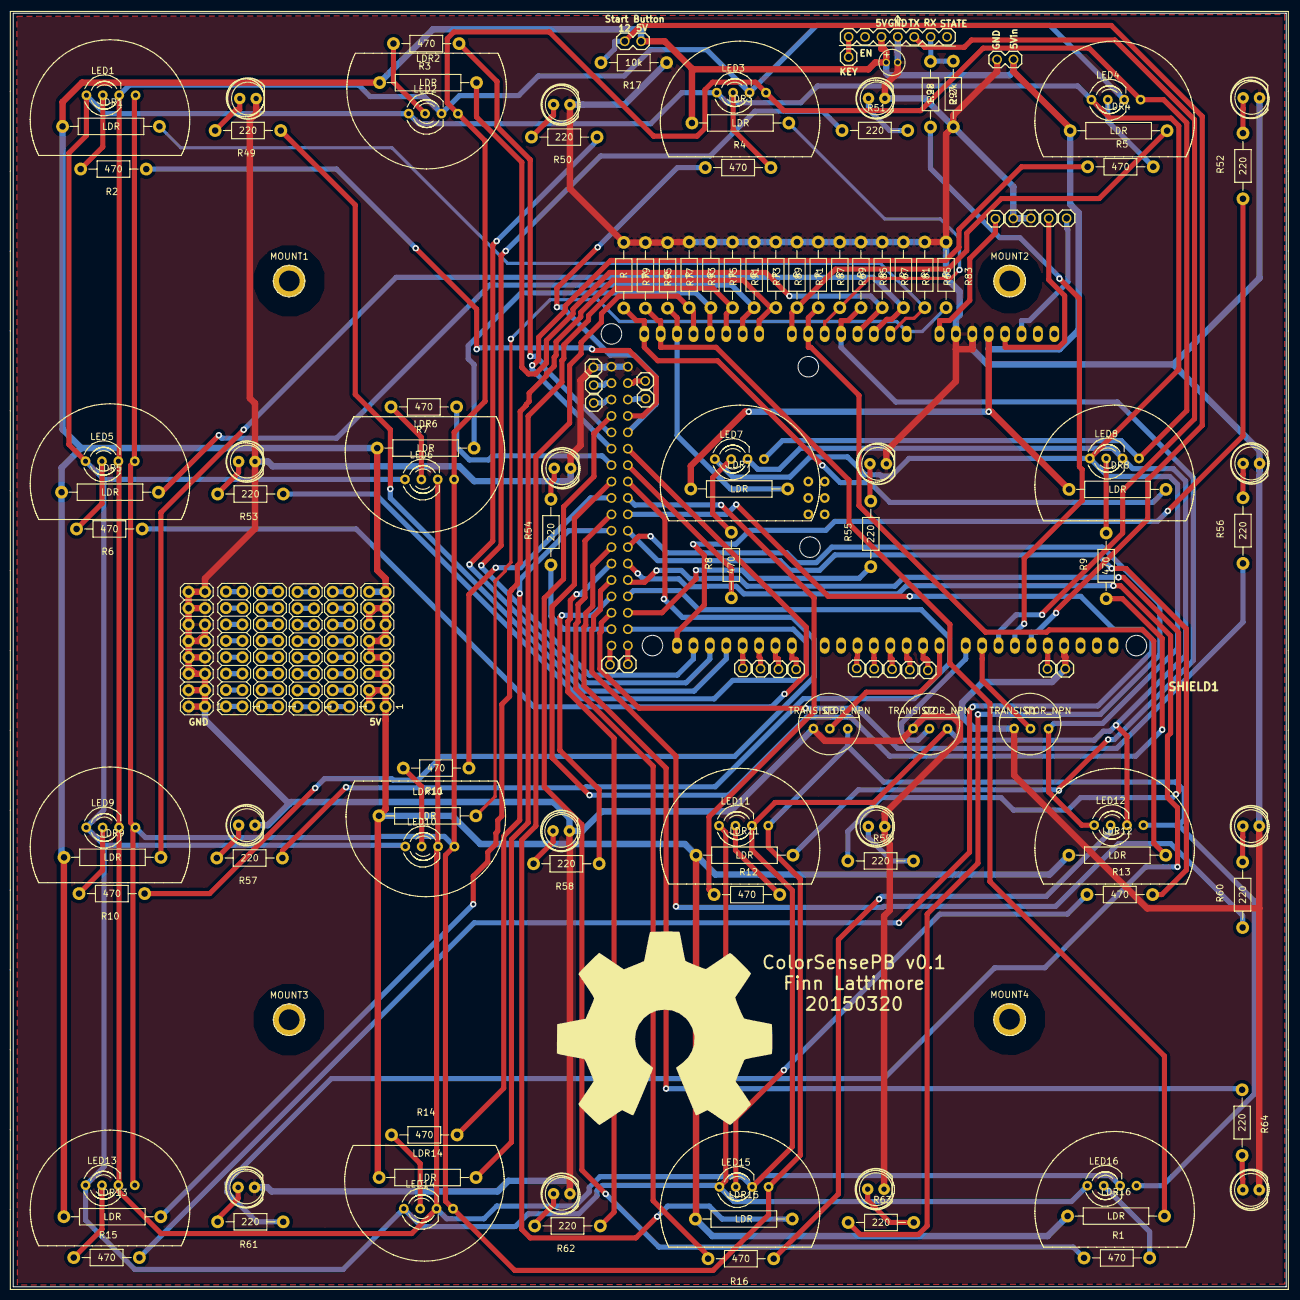
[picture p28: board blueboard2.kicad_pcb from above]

Board: 2 copper layers, 197.1 x 197.2 mm, 143 parts (1 on the bottom side), 144 nets.

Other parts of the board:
LOGO1, LOGO2: LOGO; OSWH_LOGO

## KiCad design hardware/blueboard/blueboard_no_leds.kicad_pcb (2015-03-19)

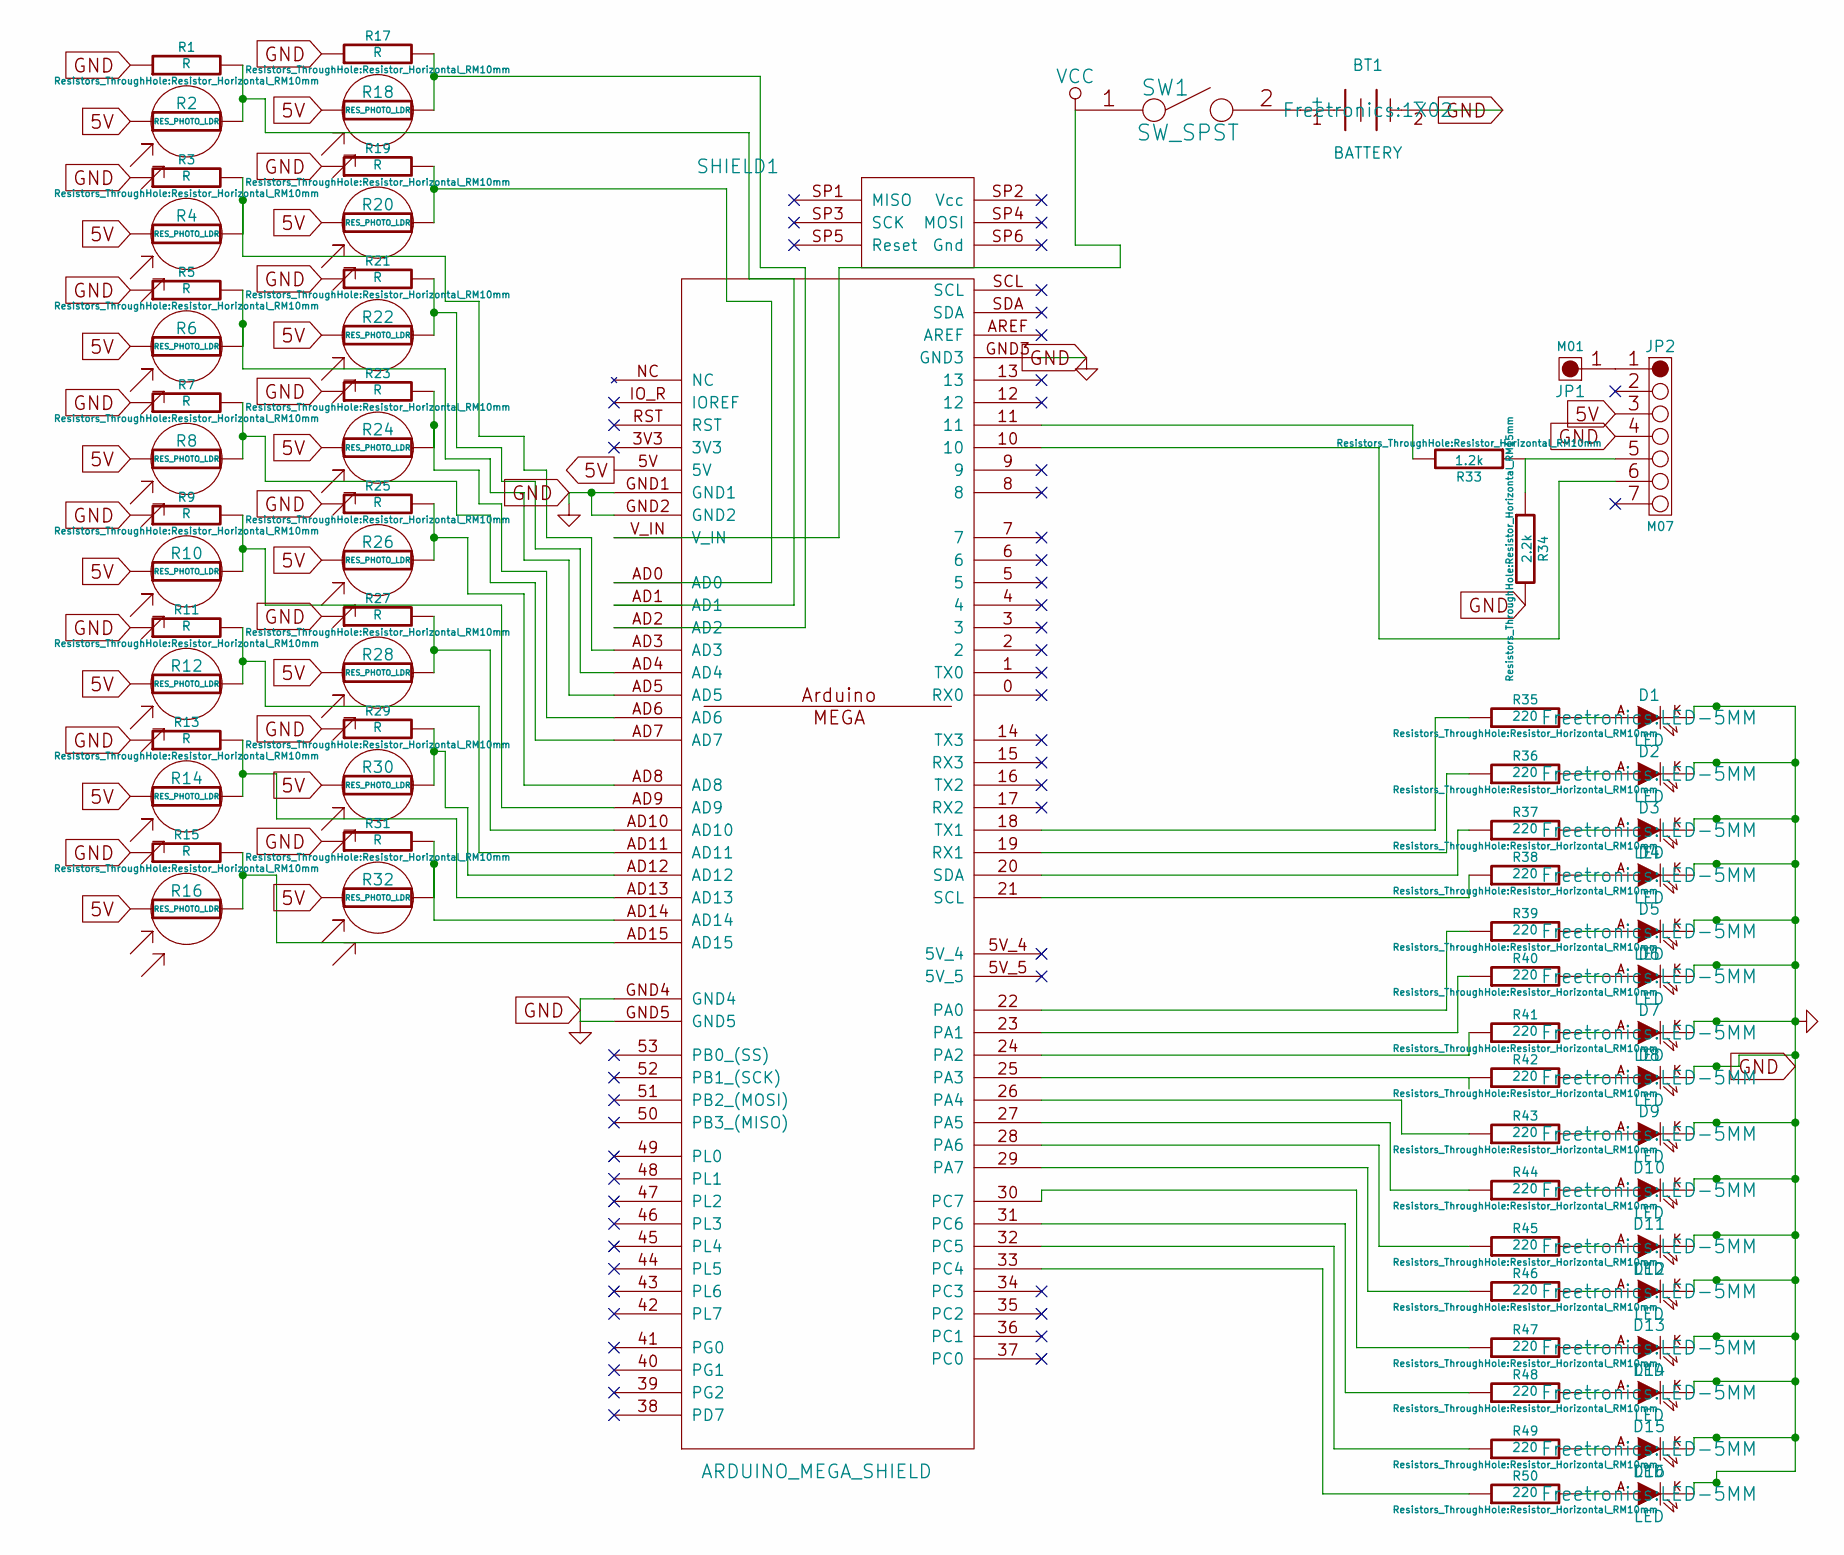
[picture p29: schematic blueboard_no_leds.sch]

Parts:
BT1: BATTERY; 1X02
D1, D2, D3, D4, D5, D6, D7, D8, D9, D10, D11, D12, D13, D14, D15, D16: LED; LED-5MM
JP1: M01; 1X01
JP2: M07; 1X07
R1, R3, R5, R7, R9, R11, R13, R15, R17, R19, R21, R23, R25, R27, R29, R31: R; Resistor_Horizontal_RM10mm
R2, R4, R6, R8, R10, R12, R14, R16, R18, R20, R22, R24, R26, R28, R30, R32: RES_PHOTO_LDR; Resistor_Horizontal_RM15mm
R33: 1.2k; Resistor_Horizontal_RM10mm
R34: 2.2k; Resistor_Horizontal_RM15mm
R35, R36, R37, R38, R39, R40, R41, R42, R43, R44, R45, R46, R47, R48, R49, R50: 220; Resistor_Horizontal_RM10mm
SHIELD1: ARDUINO_MEGA_SHIELD
SW1: SW_SPST; SW_PUSHBUTTON_TC0122

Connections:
5V: JP2.3, R2.1, R4.1, R6.1, R8.1, R10.1, R12.1, R14.1, R16.1, R18.1, R20.1, R22.1, R24.1, R26.1, R28.1, R30.1, R32.1, SHIELD1.5V
GND: BT1.2 (-), D1.K, D2.K, D3.K, D4.K, D5.K, D6.K, D7.K, D8.K, D9.K, D10.K, D11.K, D12.K, D13.K, D14.K, D15.K, D16.K, JP2.4, R1.1, R3.1, R5.1, R7.1, R9.1, R11.1, R13.1, R15.1, R17.1, R19.1, R21.1, R23.1, R25.1, R27.1, R29.1, R31.1, R34.2, SHIELD1.GND1, SHIELD1.GND2, SHIELD1.GND3, SHIELD1.GND4, SHIELD1.GND5
unnamed: BT1.1 (+), SW1.2
unnamed: D1.A, R35.2
unnamed: D2.A, R36.2
unnamed: D3.A, R37.2
unnamed: D4.A, R38.2
unnamed: D5.A, R39.2
unnamed: D6.A, R40.2
unnamed: D7.A, R41.2
unnamed: D8.A, R42.2
unnamed: D9.A, R43.2
unnamed: D10.A, R44.2
unnamed: D11.A, R45.2
unnamed: D12.A, R46.2
unnamed: D13.A, R47.2
unnamed: D14.A, R48.2
unnamed: D15.A, R49.2
unnamed: D16.A, R50.2
unnamed: JP1.1, JP2.1
unnamed: JP2.5, R33.1, R34.1
unnamed: JP2.6, SHIELD1.10
unnamed: R1.2, R2.2, SHIELD1.AD1
unnamed: R3.2, R4.2, SHIELD1.AD3
unnamed: R5.2, R6.2, SHIELD1.AD5
unnamed: R7.2, R8.2, SHIELD1.AD7
unnamed: R9.2, R10.2, SHIELD1.AD9
unnamed: R11.2, R12.2, SHIELD1.AD11
unnamed: R13.2, R14.2, SHIELD1.AD13
unnamed: R15.2, R16.2, SHIELD1.AD15
unnamed: R17.2, R18.2, SHIELD1.AD2
unnamed: R19.2, R20.2, SHIELD1.AD0
unnamed: R21.2, R22.2, SHIELD1.AD4
unnamed: R23.2, R24.2, SHIELD1.AD6
unnamed: R25.2, R26.2, SHIELD1.AD8
unnamed: R27.2, R28.2, SHIELD1.AD10
unnamed: R29.2, R30.2, SHIELD1.AD12
unnamed: R31.2, R32.2, SHIELD1.AD14
unnamed: R33.2, SHIELD1.11
unnamed: R35.1, SHIELD1.18 (TX1)
unnamed: R36.1, SHIELD1.19 (RX1)
unnamed: R37.1, SHIELD1.20 (SDA)
unnamed: R38.1, SHIELD1.21 (SCL)
unnamed: R39.1, SHIELD1.22 (PA0)
unnamed: R40.1, SHIELD1.23 (PA1)
unnamed: R41.1, SHIELD1.24 (PA2)
unnamed: R42.1, SHIELD1.25 (PA3)
unnamed: R43.1, SHIELD1.26 (PA4)
unnamed: R44.1, SHIELD1.27 (PA5)
unnamed: R45.1, SHIELD1.28 (PA6)
unnamed: R46.1, SHIELD1.29 (PA7)
unnamed: R47.1, SHIELD1.30 (PC7)
unnamed: R48.1, SHIELD1.31 (PC6)
unnamed: R49.1, SHIELD1.32 (PC5)
unnamed: R50.1, SHIELD1.33 (PC4)
VCC: SHIELD1.V_IN, SW1.1

Board: 2 copper layers, 71 parts (0 on the bottom side), 56 nets, no tracks yet.

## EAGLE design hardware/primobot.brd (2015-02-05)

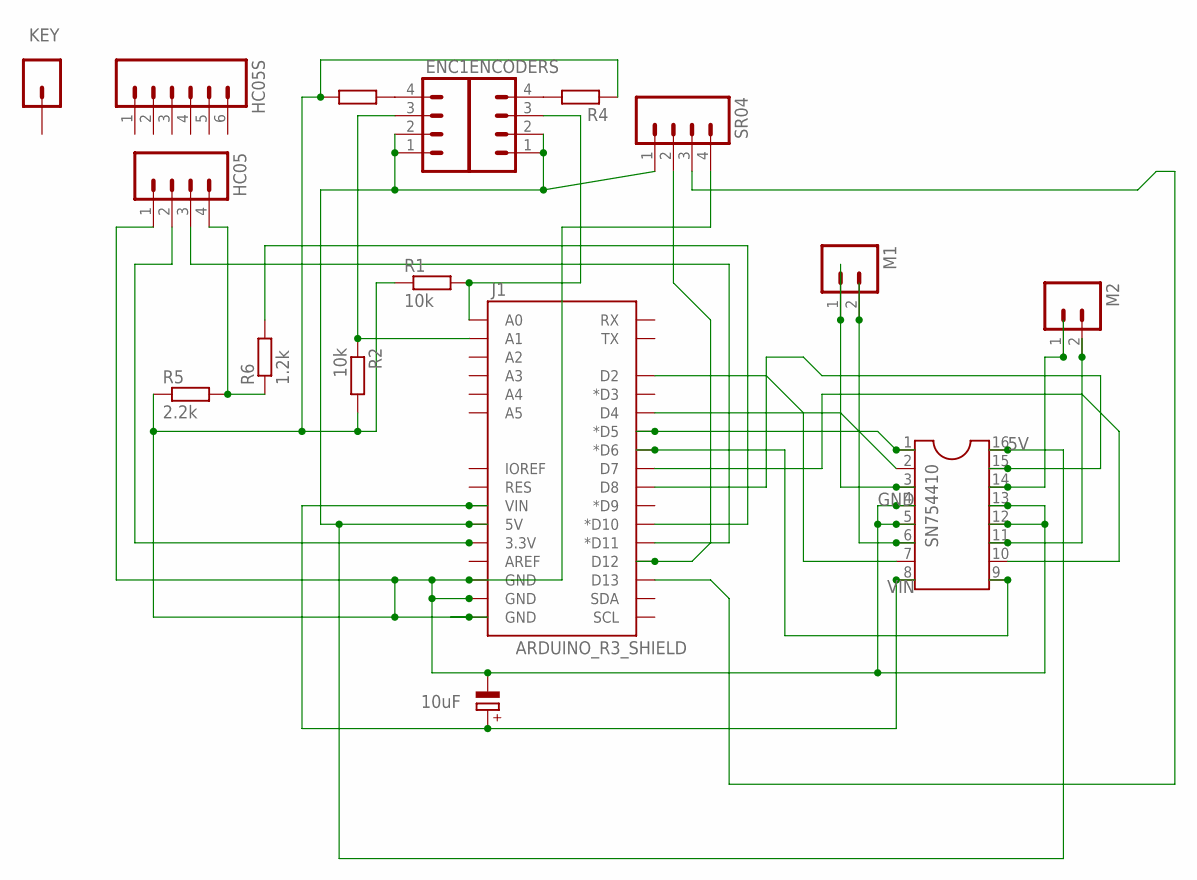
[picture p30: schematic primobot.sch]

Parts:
C1: 10uF; E5-10,5
ENC1: M04PTH; 1X04
ENCODERS: M04PTH; 1X04
HC05: M04PTH; 1X04
HC05S: M06SILK_FEMALE_PTH; 1X06
J1: ARDUINO_R3_SHIELD; UNO_R3_SHIELD
KEY: M01PTH; 1X01
M1, M2: M02PTH; 1X02
R1, R2: 10k; 0207/10
R3, R4: R-EU_0207/10; 0207/10
R5: 2.2k; 0207/10
R6: 1.2k; 0207/10
SN754410: DIL16S; SOCKET-16
SR04: M04PTH; 1X04

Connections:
5V: ENC1.1, ENC1.2, ENCODERS.1, ENCODERS.2, J1.5V, SN754410.16, SR04.1
GND: C1.-, HC05.1, J1.GND@0 (GND), J1.GND@1 (GND), J1.GND@2 (GND), R1.1, R2.2, R3.1, R4.1, R5.1, SN754410.4, SN754410.5, SN754410.12, SN754410.13, SR04.4
unnamed: J1.D5 (*D5), SN754410.1
unnamed: M1.2, SN754410.6
unnamed: M1.1, SN754410.3
unnamed: J1.D13, SR04.3
unnamed: M2.1, SN754410.14
unnamed: M2.2, SN754410.11
unnamed: J1.D7, SN754410.10
unnamed: HC05.2, J1.3.3V
unnamed: J1.D2, SN754410.7
unnamed: J1.D8, SN754410.15
unnamed: HC05.3, J1.D11 (*D11)
unnamed: J1.D6 (*D6), SN754410.9
unnamed: HC05.4, R5.2, R6.1
unnamed: J1.D10 (*D10), R6.2
unnamed: ENCODERS.4, R4.2
unnamed: ENC1.4, R3.2
unnamed: ENCODERS.3, J1.A0, R1.2
unnamed: ENC1.3, J1.A1, R2.1
unnamed: J1.D4, SN754410.2
unnamed: J1.D12, SR04.2
VIN: C1.+, J1.VIN, SN754410.8

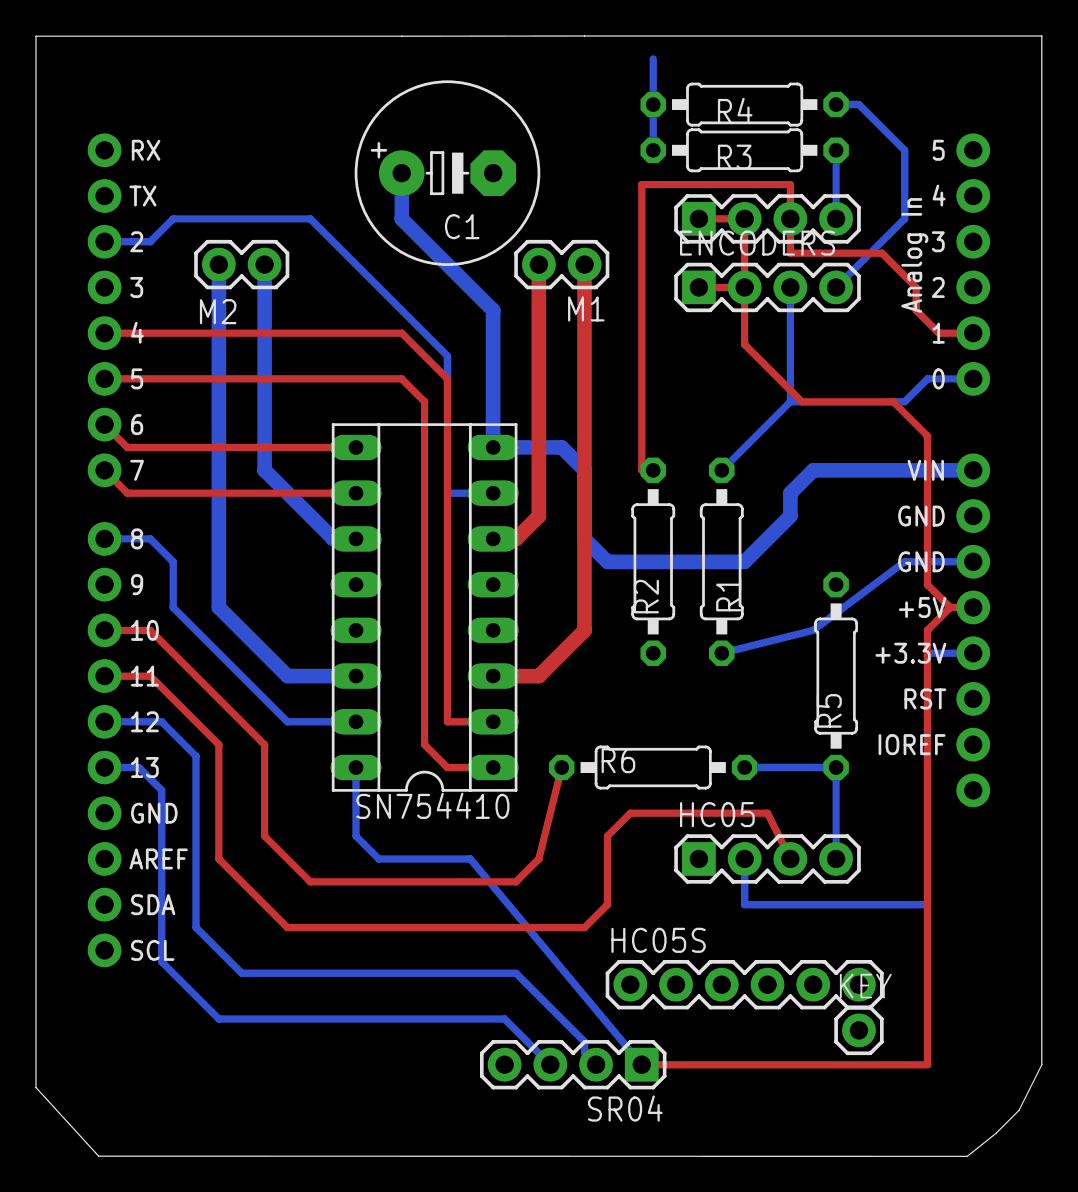
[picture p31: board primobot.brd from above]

Board: 2 copper layers, 55.9 x 62.2 mm, 17 parts (0 on the bottom side), 23 nets.

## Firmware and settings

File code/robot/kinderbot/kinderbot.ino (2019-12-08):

// This script tests the the combination of the wheels and MPU sensor to drive the robot in straight lines and 90 degree angles. 
#include <Wire.h> //I2C Arduino Library
#include <AutoPID.h>
#include <I2Cdev.h>
#include <MPU6050_6Axis_MotionApps20.h>
#include <EEPROM.h>

#define forwardTime 2000
#define leftTime 1000
#define rightTime 1000
#define DEFAULT_LEFT 117
#define DEFAULT_RIGHT 123

#define piezoPin 15
#define LEFT_FORWARD_PIN 9
#define LEFT_REVERSE_PIN 10
#define RIGHT_FORWARD_PIN 6
#define RIGHT_REVERSE_PIN 5

#define INTERRUPT_PIN 7  // interrupt 4 on pro-micro
#define LEFT 'L'
#define RIGHT 'R'
#define FORWARD 'F'

//-------------------------------------MPU contol/data--------------------------------------------
bool dmpReady = false;  // set true if DMP init was successful
uint8_t mpuIntStatus;   // holds actual interrupt status byte from MPU
uint8_t devStatus;      // return status after each device operation (0 = success, !0 = error)
uint16_t packetSize;    // expected DMP packet size (default is 42 bytes)
uint16_t fifoCount;     // count of all bytes currently in FIFO
uint8_t fifoBuffer[64]; // FIFO storage buffer

// orientation/motion vars
Quaternion q;           // [w, x, y, z]         quaternion container
VectorInt16 aa;         // [x, y, z]            accel sensor measurements
VectorInt16 aaReal;     // [x, y, z]            gravity-free accel sensor measurements
VectorInt16 aaWorld;    // [x, y, z]            world-frame accel sensor measurements
VectorFloat gravity;    // [x, y, z]            gravity vector
float euler[3];         // [psi, theta, phi]    Euler angle container
float ypr[3];           // [yaw, pitch, roll]   yaw/pitch/roll container and gravity vector

volatile bool mpuInterrupt = false;     // indicates whether MPU interrupt pin has gone high
void dmpDataReady() {
    mpuInterrupt = true;
}

//------------------------------------------------------------------------------------------------
double leftSpeed=DEFAULT_LEFT;
double rightSpeed=DEFAULT_RIGHT;

MPU6050 mpu;

double initial_heading;
double angle;
double prev_angle;
unsigned long initial_time;
unsigned long delta_time;
unsigned long lastread; //when was the sensor last read
unsigned long current_time;
unsigned long deadline;
double current_heading;
double rightOvershoot = 15;
double leftOvershoot = 15;


double setPoint = 0.0;
double speedDifference = 0;
char instruction = '0';

//int is 2 bytes.

//pid settings and gains
#define KP .5
#define KI 0
#define KD 0
AutoPID speedPID(&angle, &setPoint, &speedDifference, -5, 5 , KP, KI, KD);
int eeAddressRight = 0;
int eeAddressLeft = 2;

void setup() {
  eeAddressLeft = sizeof(rightOvershoot);
  Serial.begin(115200);
  Serial1.begin(9600);
  delay(2000);
  setupMPU();
  pinMode(LEFT_FORWARD_PIN, OUTPUT);
  pinMode(LEFT_REVERSE_PIN, OUTPUT);
  pinMode(RIGHT_FORWARD_PIN, OUTPUT);
  pinMode(RIGHT_REVERSE_PIN, OUTPUT);
  speedPID.setTimeStep(10);
  delay(10000);
  EEPROM.get(eeAddressRight,rightOvershoot);
  EEPROM.get(eeAddressLeft, leftOvershoot);
  if (isnan(leftOvershoot) || leftOvershoot < 0 || leftOvershoot > 50){
    leftOvershoot = 15;
  }
  if (isnan(rightOvershoot) || rightOvershoot < 0 || rightOvershoot > 50){
    rightOvershoot = 15;
  } 
}

void loop() {
  if (Serial1.available()){
    instruction = Serial1.read();
    Serial.write(instruction);
    switch (instruction) {
      case FORWARD:
        go_forward2();
        break;

      case LEFT:
        turn(LEFT);
        break;

      case RIGHT:
        turn(RIGHT);
        break; 
    } 
  }
  EEPROM.put(eeAddressRight,rightOvershoot);
  EEPROM.put(eeAddressLeft,leftOvershoot);
}

float angle_diff(float a1, float a2) {
  // returns a result between -180 and 180
  float result = a1 - a2;
  if (result > 180) {result = -(360 - result);}
  else if (result < -180) {result = (360 + result);}
  return result;
}

void clearMPU(){ //mpu buffer may have overflowed while we waited for the next instruction.
  mpuInterrupt = false;
  mpuIntStatus = mpu.getIntStatus();
  fifoCount = mpu.getFIFOCount();
  //if ((mpuIntStatus & 0x10) || fifoCount == 1024) {
        mpu.resetFIFO();
        fifoCount = 0;
  //}
}

void go_forward2(){
  leftSpeed = DEFAULT_LEFT;
  rightSpeed = DEFAULT_RIGHT;
  leftForward();
  rightForward();
  delay(forwardTime);
  off();
  delay(1000);
}

void go_forward() {
  //Serial.println("forward");
  clearMPU();
  initial_heading = read_heading();
  //Serial.print("initial heading:");Serial.println(initial_heading);
  initial_time = millis();
  leftSpeed = DEFAULT_LEFT;
  rightSpeed = DEFAULT_RIGHT;
  speedPID.reset();
  speedPID.run();
  leftForward();
  rightForward();
  clearMPU();
  while ((millis() - initial_time) < forwardTime) {
      current_heading = read_heading(); 
      if (current_heading < 1000) {
        angle = angle_diff(initial_heading,current_heading);
        // positive angle => turn left, negative angle => turn right
        speedPID.run();
        leftSpeed = DEFAULT_LEFT + speedDifference;
        rightSpeed = DEFAULT_RIGHT - speedDifference;
        leftForward();
        rightForward();
        //Serial.print("input:");Serial.print(angle);Serial.print(" setpoint:");Serial.print(setPoint);Serial.print(" output:");Serial.println(speedDifference);
        Serial.print(angle);Serial.print(',');Serial.print(leftSpeed);Serial.print(',');Serial.println(rightSpeed);
      }
  }
  off();
  speedPID.stop();
  delay(1000);
}

void turn(char direct){
  leftSpeed = DEFAULT_LEFT;
  rightSpeed = DEFAULT_RIGHT;
  //Serial.println(direct);
  clearMPU();
  initial_heading = read_heading_retry(5);
  double *overshoot;  
  if (direct == LEFT) {
     leftReverse();
     rightForward();
     overshoot = &leftOvershoot; // does this mean that changing overshoot changes the value of leftOvershoot?
  }
  else {
      leftForward();
      rightReverse();
      overshoot = &rightOvershoot;
  }
  double target_angle = 90.0 - *overshoot;
  initial_time = millis();  
  deadline = millis() + leftTime;
  lastread = millis();
  angle = 0; 
  while (millis() < deadline) {
     current_heading = read_heading(); 
     if (current_heading < 1000){
       prev_angle = angle;
       angle = abs(angle_diff(initial_heading,current_heading));
       current_time = millis();
       delta_time = current_time - lastread;
       lastread = current_time;
       //Serial.print(delta_time);Serial.print(',');Serial.println(angle);
       if (angle > target_angle) {
         break;
       }
     } 
  }  
  off();
  deadline = millis()+300; //allow 300ms for deceleration
  while (millis() < deadline) { 
    current_heading = read_heading(); 
    if (current_heading < 1000){
       prev_angle = angle;
       angle = abs(angle_diff(initial_heading,current_heading));
       current_time = millis();
       delta_time = current_time - lastread;
       lastread = current_time;
       //Serial.print(delta_time);Serial.print(',');Serial.println(angle);
    } 
  }
  //clearMPU();
  current_heading = read_heading_retry(5); // want to have decreased by 90.
  angle = abs(angle_diff(initial_heading,current_heading));
  *overshoot += angle - 90;
  current_time = millis();
  delta_time = current_time - lastread;
  //Serial.print(delta_time);Serial.print(',');Serial.println(angle);
  //Serial.print("OVS");Serial.print(leftOvershoot);Serial.print(':');Serial.println(rightOvershoot);
  
}

float read_heading_retry(int retries){
  int attempts = 0;
  float result = 1000;
  while (attempts <= retries) {
    result = read_heading();
    if (result < 1000){
      return result;
    }
    attempts +=1;
  }
  return result;
}

double last_heading = 1000;
int skipped = 0;
float read_heading(){
    while (!mpuInterrupt && fifoCount < packetSize) {} //wait for data to be available
    float heading = 1000;
    mpuInterrupt = false;
    mpuIntStatus = mpu.getIntStatus();

    // get current FIFO count
    fifoCount = mpu.getFIFOCount();

    // check for overflow (this should never happen unless our code is too inefficient)
    if ((mpuIntStatus & 0x10) || fifoCount == 1024) {
        // reset so we can continue cleanly
        mpu.resetFIFO();
        //Serial.println(F("FIFO overflow!"));
    // otherwise, check for DMP data ready interrupt (this should happen frequently)
    } else if (mpuIntStatus & 0x02) {
        // wait for correct available data length, should be a VERY short wait
        while (fifoCount < packetSize) {fifoCount = mpu.getFIFOCount();}

        int packetsRead = 0;
        while (fifoCount >= packetSize) {

          // read a packet from FIFO
          mpu.getFIFOBytes(fifoBuffer, packetSize);
          
          // track FIFO count here in case there is > 1 packet available
          // (this lets us immediately read more without waiting for an interrupt)
          fifoCount -= packetSize;
          packetsRead ++;
        }
        
        // display Euler angles in degrees
        mpu.dmpGetQuaternion(&q, fifoBuffer);
        mpu.dmpGetGravity(&gravity, &q);
        mpu.dmpGetYawPitchRoll(ypr, &q, &gravity);
        heading = (ypr[0] * 180/M_PI);
    }
  //if ((last_heading < 1000) & (abs(angle_diff(last_heading,heading)) > 30) & (skipped < 10)){
  //  heading = 1024;
  //  skipped +=1;
  //} else {
  //  last_heading = heading;
  //  skipped = 0;
  //}
  return heading;
}

void setupMPU() {
    // join I2C bus (I2Cdev library doesn't do this automatically)
    Wire.begin();
    Wire.setClock(400000); // 400kHz I2C clock. Comment this line if having compilation difficulties
    // initialize device
    //Serial.println(F("Initializing I2C devices..."));
    mpu.initialize();
    pinMode(INTERRUPT_PIN, INPUT);

    // verify connection
    //Serial.println(F("Testing device connections..."));
    //Serial.println(mpu.testConnection() ? F("MPU6050 connection successful") : F("MPU6050 connection failed"));
    delay(2000);
    // load and configure the DMP
    //Serial.println(F("Initializing DMP..."));
    devStatus = mpu.dmpInitialize();
    // supply your own gyro offsets here, scaled for min sensitivity
    mpu.setXGyroOffset(33);
    mpu.setYGyroOffset(-25);
    mpu.setZGyroOffset(-47);
    mpu.setZAccelOffset(5094); // 1688 factory default for my test chip

    // make sure it worked (returns 0 if so)
    if (devStatus == 0) {
        // turn on the DMP, now that it's ready
        //Serial.println(F("Enabling DMP..."));
        mpu.setDMPEnabled(true);

        // enable Arduino interrupt detection
        //Serial.println(F("Enabling interrupt detection..."));
        attachInterrupt(digitalPinToInterrupt(INTERRUPT_PIN), dmpDataReady, RISING);
        mpuIntStatus = mpu.getIntStatus();

        // set our DMP Ready flag so the main loop() function knows it's okay to use it
        //Serial.println(F("DMP ready! Waiting for first interrupt..."));
        dmpReady = true;
        // get expected DMP packet size for later comparison
        packetSize = mpu.dmpGetFIFOPacketSize();
    } else {
        // ERROR!
        // 1 = initial memory load failed
        // 2 = DMP configuration updates failed
        // (if it's going to break, usually the code will be 1)
        //Serial.print(F("DMP Initialization failed (code "));
        //Serial.print(devStatus);
        //Serial.println(F(")"));
    }
}

void off(){
  analogWrite(LEFT_FORWARD_PIN,0);
  analogWrite(RIGHT_FORWARD_PIN,0);
  analogWrite(LEFT_REVERSE_PIN,0);
  analogWrite(RIGHT_REVERSE_PIN,0);
}

void leftForward(){
  analogWrite(LEFT_REVERSE_PIN,0);
  analogWrite(LEFT_FORWARD_PIN,leftSpeed);
}

void rightForward(){
  analogWrite(RIGHT_REVERSE_PIN,0);
  analogWrite(RIGHT_FORWARD_PIN,rightSpeed);
}

void leftReverse(){
  analogWrite(LEFT_FORWARD_PIN,0);
  analogWrite(LEFT_REVERSE_PIN,leftSpeed);
}

void rightReverse(){
  analogWrite(RIGHT_FORWARD_PIN,0);
  analogWrite(RIGHT_REVERSE_PIN,rightSpeed);
}

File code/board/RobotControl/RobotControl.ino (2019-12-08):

#include <SoftwareSerial.h>
#include <limits.h>
#include<math.h>
#define inputs 16
#define repeats 10 // the number of times to measure each analog input - to reduce variance

// Define which pin controls the each color of the RGB leds
#define red 9
#define green 8
#define blue 7
#define FUNCTION 'C'
#define NOOP 'N'


SoftwareSerial mySerial(10, 11); // RX - connect to orange TX line from HC05, TX - connect to green recive line on HCO5

int centers[4][3] = {
   {-75,14,114},
   {-91,-31,-40},
   {72,-62,-43},
   {94,78,-31},
};

int average_brightness[16][3] = {
   {507,588,255},
   {684,686,365},
   {709,643,295},
   {652,670,342},
   {694,410,420},
   {625,439,460},
   {696,508,496},
   {590,361,339},
   {710,606,282},
   {651,661,333},
   {627,663,366},
   {660,632,309},
   {615,520,90},
   {650,661,304},
   {715,699,371},
   {681,559,277},
};





int leds[] = {36,40,44,48,47,43,39,35,34,38,42,46,49,37,41,45};
int ldrs[] = {A8,A2,A9,A1,A3,A11,A0,A10,A12,A4,A13,A5,A14,A6,A15,A7};
int redLeds[] =  {30,26,22,18,19,23,27,31,32,28,24,20,33,29,25,21};


int colors[3] = {red,green,blue};
int light[16][4]; // stores ldr values - background,red,green,blue
int program[16];

int up_d = 30; // time to leave led on before reading value
int down_d = 300; //time to turn off before reading next value
int dark = 20; // max value of ldr with no tile on top - this needs to be tile dependent ...


int buttonPin = 12;
int buttonState = 0;
int currentInstruction = -1;
int dispatchPoint = -1; // if we are in the function, used to store where we came from so we can return back there


void setup()  
{
  Serial.begin(9600);
  mySerial.begin(9600);
  pinMode(buttonPin,INPUT);
  pinMode(red,OUTPUT);
  pinMode(blue,OUTPUT);
  pinMode(green,OUTPUT);
  for (int i = 0; i < inputs; i ++) {
    pinMode(leds[i],OUTPUT); 
    pinMode(redLeds[i],OUTPUT);
  }
}
char instruction(int indx){
   if (indx == 0){return 'L';}
   if (indx == 1){return 'C';}
   if (indx == 2){return 'F';}
   if (indx == 3){return 'R';}
   return 'N';
}

void loop() // run over and over
{
  if (currentInstruction < 0) {
      // read the background light
      readLDRs(0); 
      
      // turn on indicator leds where there is a tile
      for (int i = 0; i < inputs; i++){
        if (light[i][0] < dark){
          digitalWrite(redLeds[i],HIGH);
        } else {
          digitalWrite(redLeds[i],LOW);
        }
      }
       
      // read state of button
      int b = digitalRead(buttonPin);
      if (b != buttonState){
        buttonState = b;
        if (buttonState == 1){
          Serial.println("BUTTON PRESSED!");
          currentInstruction = 0;
           // set all LEDs to low
          for (int i = 0; i < inputs; i ++) {
             digitalWrite(redLeds[i],LOW); 
          }
          // read current program
          detectColors();
        }
      }
    
  } else { 
    int iSet = program[currentInstruction]; // what was in the place of the current instruction when the button was pushed
    int iNow = detectTileColor(currentInstruction);// read what is currently happing at the specified tile
       
    if (iSet != iNow) {
      currentInstruction = -1; //terminating as program changed
    } else {
        char action = instruction(iSet);
        if (action != NOOP) {
          digitalWrite(redLeds[currentInstruction],HIGH);
          if (action != FUNCTION){
              Serial.println(action);
              mySerial.println(action);
              delay(1000);
          } else {
            delay(200);
          }
          digitalWrite(redLeds[currentInstruction],LOW);
        }
        currentInstruction ++;
                
        if (currentInstruction == 12) { // end of program - terminate
          currentInstruction = -1;
        } else if (action == FUNCTION) {
           Serial.println("FUNCTION CALL");
           dispatchPoint = currentInstruction;
           currentInstruction = 12; 
        }   else if (currentInstruction > 15) { //end of function
          currentInstruction = dispatchPoint;
          dispatchPoint = -1;
        }      
     }
  }
}






void readLDRs(int colorIndx){ //color indx 0 = background, 1=red, 2 = green, 3 = blue
    for (int i = 0; i < 16; i++) {
      int input = ldrs[i];
      light[i][colorIndx] = analogRead(input);
    }  
}

  
void readTileColors(){
  // reads the intensity of light reflected for each spot where a tile is placed and stashes values in light array
  readLDRs(0);
  for (int c = 0; c < 3; c ++) { 
      int color = colors[c];
      colorOn(color);     
      delay(up_d);
      readLDRs(c+1);
      off();
      delay(down_d);
  }
}


void detectColors(){
   readTileColors();
   int rgb[16][3]; // stores normalised rgb values for each tile slot
   for (int tile=0; tile < 16; tile ++){
     int matchColor = -1;
     if (light[tile][0] < dark){ 
       for (int i = 0; i < 3; i++){
          rgb[tile][i] = light[tile][i+1] - average_brightness[tile][i]; // +1 as first is background
       }     
       int closest = INT_MAX;
       for (int tileColor = 0; tileColor < 4; tileColor ++) {
          unsigned int d = pow(rgb[tile][0] - centers[tileColor][0],2) 
                     + pow(rgb[tile][1] - centers[tileColor][1],2)
                     + pow(rgb[tile][2] - centers[tileColor][2],2);
          if (d < closest){
             closest = d;
             matchColor = tileColor; 
          }
       }
     }
     program[tile] = matchColor; 
   } 
}

int detectTileColor(int tile){
  // reads into global rgb variable  
  int background = analogRead(ldrs[tile]);
  if (background > dark){
    return -1; 
  } 
  int rgb[3];
  for (int c = 0; c< 3; c++) {
     int color = colors[c];
     colorOnOne(color,tile);
     delay(up_d);
     rgb[c] = analogRead(ldrs[tile])- average_brightness[tile][c];
     off();
     delay(down_d); 
  }
  // now find the closest match for the reflection response
  int matchColor = -1;     
  int closest = INT_MAX;
  for (int tileColor = 0; tileColor < 4; tileColor ++) {
    unsigned int d = pow(rgb[0] - centers[tileColor][0],2) 
                     + pow(rgb[1] - centers[tileColor][1],2)
                     + pow(rgb[2] - centers[tileColor][2],2);    
    if (d < closest){
       closest = d;
       matchColor = tileColor; 
    }
  }
  return matchColor;  
}

void colorOnOne(int color, int tile){
    digitalWrite(red,LOW);
    digitalWrite(green,LOW);
    digitalWrite(blue,LOW);
    digitalWrite(color,HIGH);
    digitalWrite(leds[tile],HIGH);
}

void colorOn(int color){
    digitalWrite(red,LOW);
    digitalWrite(green,LOW);
    digitalWrite(blue,LOW);
    digitalWrite(color,HIGH);
    for (int i = 0; i < 16; i++) {
      if (light[i][0] < dark){ //if it is dark ie, there is a tile there...
        digitalWrite(leds[i],HIGH);
      }
    }
}

void off(){
    digitalWrite(red,LOW);
    digitalWrite(green,LOW);
    digitalWrite(blue,LOW);
    for (int i = 0; i < 16; i++) {
      digitalWrite(leds[i],LOW);
    }
}

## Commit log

2014-12-01 adds svg degin files for board
2014-12-01 enlarges space for resistor in programming tiles
2014-12-19 adds primo board code with median calculation. There is a bug in array access
    [primoboard.ino]
2014-12-20 creates directory structure and adds code scripts for testing bluetooth communication
    [primoboard_1mm.dxf, primoboard_3mm_sheet1.dxf, primoboard_3mm_sheet2.dxf]
2014-12-20 gets primoboard codeto the point where leds light when tiles are inserted, code is executed when button is pushed and leds indicate which opperation is currently being executed. instruction execution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
2014-12-21 adds first version of code for robot - just recieves instructions from board over bluetooth and prints them to Serial
2015-02-05 lots of changes
    [BallCasterV2.scad, BallCasterV2.stl, BallCasterV2_1.stl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]
2015-02-14 too many changes to remember
    [bb_auto_with_ground.dsn, bb_auto_with_ground.kicad_pcb, blueboard.kicad_pcb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]
2015-02-14 state when board was cncd
    [blueboard01.sch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]
2015-02-22 prior to starting over on cnc board
    [blueboard_cnc.kicad_pcb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]
2015-03-19 round 2 of board design
    [$blueboard2.sch, blueboard.kicad_pcb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]
2015-03-21 state when board sent to manufacture
    [$blueboard2.sch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]
2015-05-04 updated svgs to fit manufactured board. Reconnected resistors in schematica
    [blueboard2.sch]
2015-05-04 adds code to test pcb from arduino sketchbook
    [$blueboard2.sch]
2015-10-23 updates to printed circuit board. Still missing programming access, switch mount and charging access
2015-11-07 changes from old laptop
    [$blueboard2.sch, finnprimo3_3mm.dxf]
2015-11-07 fixes indicator test so LEDs come on in board order
    [indicatorLEDTest_PCB.ino]
2015-11-07 Updates RGBLEDTest to pins for printed PCB
2015-11-07 adds LDRTest, configured for printed pcb
2015-11-07 adds README for board callibration
2015-11-24 completes refactor of readdata.py and utils.py to avoid use of numpy/scipy
    [readdata.py, utils.py]
2015-11-24 removed old files
    [color2.csv, color_data2.csv, light.csv]
2015-11-24 moves things into a more logical directory structure
    [color2.csv, color_data2.csv]
2018-04-01 updates board svg top to have tiles go all the same direction
2018-04-01 makes square pegs for board holder to glue in
2018-04-02 removes double cut from tiles in second row
2018-04-02 splits board design into 600 by 400 mm sheets
    [board_sheet1.dxf, board_sheet2.dxf]
2018-04-11 adds bottom half of tile smaller than hole dimension
2018-04-11 adds cutout for switch and power in
2018-04-11 improves design to attach bottom of board
2018-04-11 adds version of board with cross support for pcb
2018-04-11 cleans up board design files
    [board.dxf, board_sheet1.dxf, board_sheet2.dxf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]
2018-04-11 cleans up svgs for robot
    [bot2_01.dxf, bot2_02.dxf, bot2_03.dxf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]
2018-04-13 completes robot design, adds cross support for pcb
    [board_sheet1.dxf, board_sheet2_with_cross_support.dxf, clear_acrylic.dxf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]
2018-04-13 major updates to color sensing code
    [board_response_data201512121125.csv, board_response_data201512121426.csv, color2.csv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]
2018-04-15 removes cable port
2018-04-15 moves mount point for kinder backward
2018-04-15 fixes cutout for switch
2018-04-15 adds script to test wheels on robot
2018-04-17 adds arduino sketch to pair hc05 bluetooth modules
2018-04-17 starts on docs, cleans up old stuff
    [bluetooth_setup.fzz, robot.fzz]
2019-12-08 adds README for board setup
2019-12-08 cleans up board code
2019-12-08 updates to include arduino code generation in read.py
2019-12-08 local changes made oh so long ago
    [kinderbot.kicad_pcb, kinderbot.sch, robot.dxf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]

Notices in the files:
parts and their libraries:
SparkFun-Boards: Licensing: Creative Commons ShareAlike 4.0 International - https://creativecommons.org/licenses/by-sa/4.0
